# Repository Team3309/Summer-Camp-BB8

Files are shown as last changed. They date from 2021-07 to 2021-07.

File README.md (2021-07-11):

  
This work is licensed under a [Creative Commons Attribution-NonCommercial-ShareAlike 4.0 International License](http://creativecommons.org/licenses/by-nc-sa/4.0/).

# Overview

This is a remix of [DIY Machine's 3D printable BB8 robot](https://www.thingiverse.com/thing:2749613/files).

It replaces the stock Arduino Uno with an ESP32 DevKit and includes a reed switch to turn the robot on/off. In addition, a generic L298N motor controller board replaces the original motor shield

# Bill Of Materials

| Qty. | Name | Link |
| --- | --- | --- |
| 10 | 6 * 3mm Neodymium magnets | [Amazon](https://www.amazon.com/DIYMAG-6x3mm-Refrigerator-Premium-Brushed/dp/B07KZQGWNN/)
| 1 | Styrofoam hemisphere |
| 1 | Reed switch |
| 1 | L298N motor controller board |
| 1 | 3.3V Low-dropout regulator board |
| 1 | DOIT ESP32 DevKit v1 |
| 1 | 4*AA Battery harness |
| 2 | Geared 6v motors | [Amazon](https://www.amazon.com/Electric-Magnetic-Gearbox-Plastic-Yeeco/dp/B07DQGX369/) |
| 2 | 2.75in wheels | (included with motors) |
| 2-4 | .25in 4-40 Machine screws |
| 1 | Can of white spray paint |
| 1-2 fl oz | White acrylic paint |
| | Assorted sharpies |
| 1 | Roll of clear gift wrap tape |
| ≥5 | Small zipties |
| ~1in<sup>2<sup> | Low friction PTFE tape |
| A few | Male-male wires |
| A few | Female-female wires |
| One of each | Printed parts | [CAD/STLs](https://github.com/Team3309/Summer-Camp-BB8/tree/main/CAD/STLs) |

# Assembly

## Step 0: Prepping shells and decoration

1. Sand the inside and outside of the shells so that the chassis and head can both slide freely on them

2. Spray paint the outside of the shells

3. Hotglue the styrofoam hemisphere to the head, then use white acrylic paint to coat the assembly

4. Use the stand as a stencil to sharpie BB8 patterns onto the shell

## Step 1: Installing motors and motor controller

1. As shown in DIY Machines' video, put the motors in the chassis and secure them with zip ties

2. Ziptie the motor controller bracket to the neck/mast of the chassis

3. Use the screws to secure the motor controller **with the heatsink facing down**

## Step 2: Installing the reed switch

1. Use the jaws of a pair of calipers to gently bend the leads of the reed switch
    - Make sure the side with the circle artifacts from the injection mold is facing away from the leads

2. Solder a pair of wires (any color, preferably red) to the leads
    - They should be about 4 inches long, better to make it long and cut later

3. Insert the reed switch into the slot on the top of the neck/mast. **Be careful not to bend the leads**, lest you risk breaking the fragile reeds inside

## Step 3: Wiring and cable management

1. Connect the components according to the wiring diagram
    - To connect multiple wires to the screw terminals on the motor controller, strip the ends of the wires and twist them together
    - The GND pin of the LDO needs to be connected directly to the GND pin on the ESP32 board
        - If negative from the battery, GND on the LDO, and GND on the ESP32 are connected with separate wires to the GND terminal of the motor controller, then electrical noise causes the ESP32 to intermittently shut off, which is bad (duh)
        - To solve that issue, strip the opposite end of the wire that is connected to the ESP32's ground pin and (gently) shove that end into the connector on the LDO's ground pin, then put that connector back on the LDO pin

2. Use a ziptie to secure the ESP32 board to the chassis ***TODO: example photo***

3. Do your best to round up all the cables so that none touch the wheels or shell of the robot

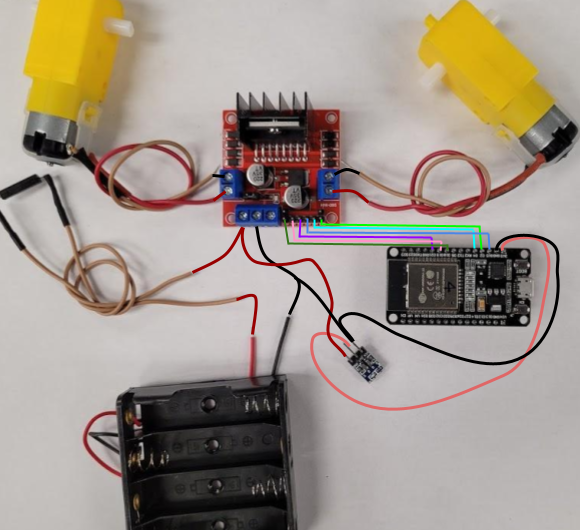
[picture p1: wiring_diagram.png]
Wiring Diagram

[Source for the above image](https://docs.google.com/presentation/d/1EXfWSO4wvMNs9FQZjlcnMrIVXtP51tsHmDwQ05yeIWY/edit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)

## Step 4: Installing neck and head magnets

1. Glue (try superglue if possible) two magnets in each slot on top of the neck
    - Make sure that they are all in the same orientation

2. Place small squares of PTFE tape on each exposed magnet

3. Put a half of the shell on top of the neck, then put a piece of wax paper

4. Stick three magnets to the ones in the neck (through the shell)

5. Apply hot glue to those magnets, then **quickly**, before the glue cools, place the head as straight as possible, facing forward

6. Once the magnets on the head are securely in place, glue another one in between the two in the front of the head
    - This is to trigger the reed switch when the head is in place

7. After the glue has fully cooled, place small squares of PTFE tape on each exposed magnet

## Step 5: Flash ESP32 board

- See /Code/README.md

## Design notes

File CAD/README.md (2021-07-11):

# 3D Printed Parts

| Qty. | Name | Source file | Notes |
| ---- | ---- | --- | ----- |
| 1 | BB8 Chassis | [Tinkercad](https://www.tinkercad.com/things/54Emxx3GyOb) (See below) |
| 1 | Motor Controller Bracket | [Onshape]()
| 1 | Grooved_Half_V2 | None |
| 1 | Tounged_Half_V2 | None |
| 1 | Head_V6_modified | [Autodesk Inventor](https://github.com/Team3309/Summer-Camp-BB8/tree/main/CAD/Source/Head_V6_Modified.ipt)
| 1 | Sensor | none | Optional, used as decoration on the head |
| 1 | Eye | none | Optional, used as decoration on the head |

<iframe width="725" height="453" src="https://www.tinkercad.com/embed/54Emxx3GyOb?editbtn=1" frameborder="0" marginwidth="0" marginheight="0" scrolling="no"></iframe>

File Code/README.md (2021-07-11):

# Flashing instructions

## Step 1: Setting up Arduino IDE

1. Download and install the [Arduino IDE](https://www.arduino.cc/en/software)

2. Go to **File > Preferences** (or press ctrl+,) and paste "https://dl.espressif.com/dl/package_esp32_index.json" into the "Additional Board Manager URLs" field, then click "OK"

3. Go to **Tools > Board > Boards Manager**, use the search bar on the top to find "esp32" and install **"esp32 by Espressif Systems"**

4. Go to **Tools > Manage Libraries...** and search "Dabble", then install "**DabbleESP32**"
    - The plain "Dabble" library will not work in this case, you must use "DabbleESP32"

5. Download [this](https://github.com/ERROPiX/ESP32_AnalogWrite/archive/refs/heads/master.zip) library, then go to **Sketch > Include Library > Add .ZIP Library...** and navigate to and select the the .zip archive that just downloaded

## Step 2: Flashing the board

1. Download and open (**File > Open**) ["BB8_dabble.ino"](https://github.com/Team3309/Summer-Camp-BB8/blob/main/Code/BB8_dabble.ino)
    - Optionally, find `Dabble.begin("BB8_xx");` and change the contents of the `""` to be whatever you want the robot to appear as on the pairing screen

2. Make sure that noting is powering the robot by removing one of the batteries

3. Go to **Tools > Board** and select **DOIT ESP32 DEVKIT V1**

4. Plug the ESP32 board into your computer with a micro-USB cable

5. Go to **Tools > Port** and select "COMx"
    - If there are multiple COM ports, you may need to use trial and error to find the right one (i.e continue with the next steps and if you get errors like "board not found", then switch ports and try again)

6. If you did everything correctly, then when you press the checkmark in the top left corner, the code should compile with no errors.

7. If it compiled with no problems, then flash the code onto the ESP32 by clicking the "upload" (arrow) button directly next to the checkmark

## Step 3: It's alive!

1. Unplug the USB cable, then power on the robot by replacing the batteries and putting the head in place on the neck

2. Download the Dabble app on your phone if you haven't done so already ([iOS](https://apps.apple.com/us/app/dabble-bluetooth-controller/id1472734455), [Android](https://play.google.com/store/apps/details?id=io.dabbleapp))

3. Launch the app and press the pair button (a plug and socket) in the top right corner

4. Find "BB8_xx" and pair to that, then open the "Controller" screen

5. Press the up button on the controller
    - The reed switch is in the front of the robot
    - If the left wheel spins backward, then change `#define LEFT_MOTOR_INVERTED false` to `#define LEFT_MOTOR_INVERTED true` and flash the updated code onto the ESP32 board again
    - If the right wheel spins backward, then change `#define RIGHT_MOTOR_INVERTED false` to `#define RIGHT_MOTOR_INVERTED true` and flash the updated code onto the ESP32 board again
    - Alternatively, switch the polarity of the inverted motor(s)

6. Press the right button on the controller
    - If the left wheel spins backward and the right wheel spins forward (i.e. robot spins counterclockwise), then move the wires from the left and right motors to the opposite set of terminals on the motor controller and repeat the last step

7. Finally, put the robot chassis inside the shells and tape them closed. Then attach the head to the top of the robot to power it on
    - Chances are that the reed switch will not stay reliably closed and the robot will loose connection as soon as it moves at all. In that case, tape/glue annother magnet on top of the reed switch so that it is always triggered

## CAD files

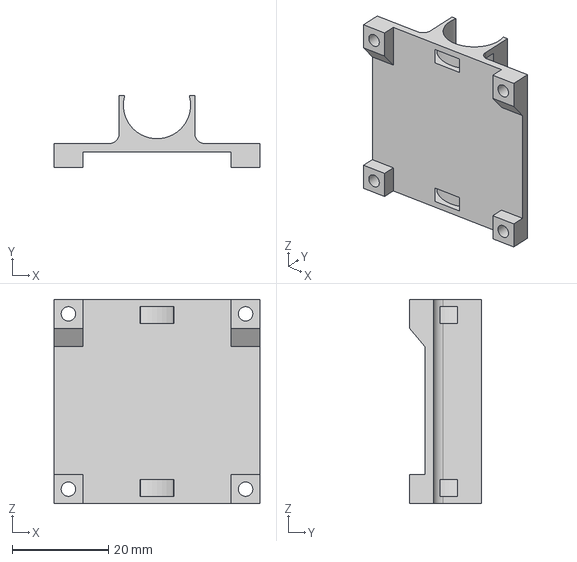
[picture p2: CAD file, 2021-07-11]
CAD/STEP/Motor Controller Bracket.step
42.9 x 15.0 x 42.5 mm

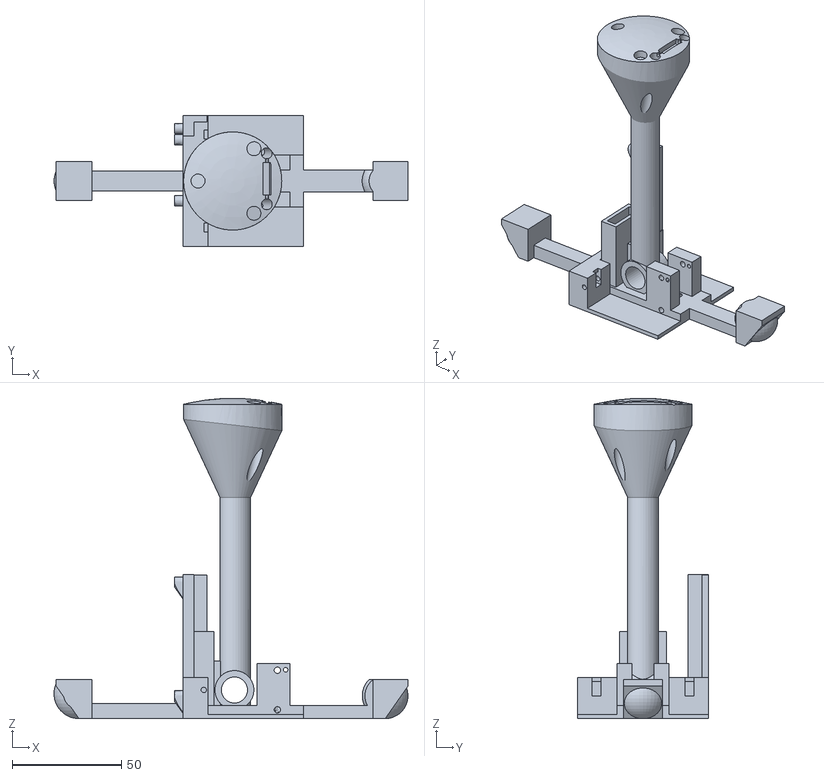
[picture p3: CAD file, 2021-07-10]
CAD/STL/BB8 Chassis.stl
162.2 x 60.0 x 146.8

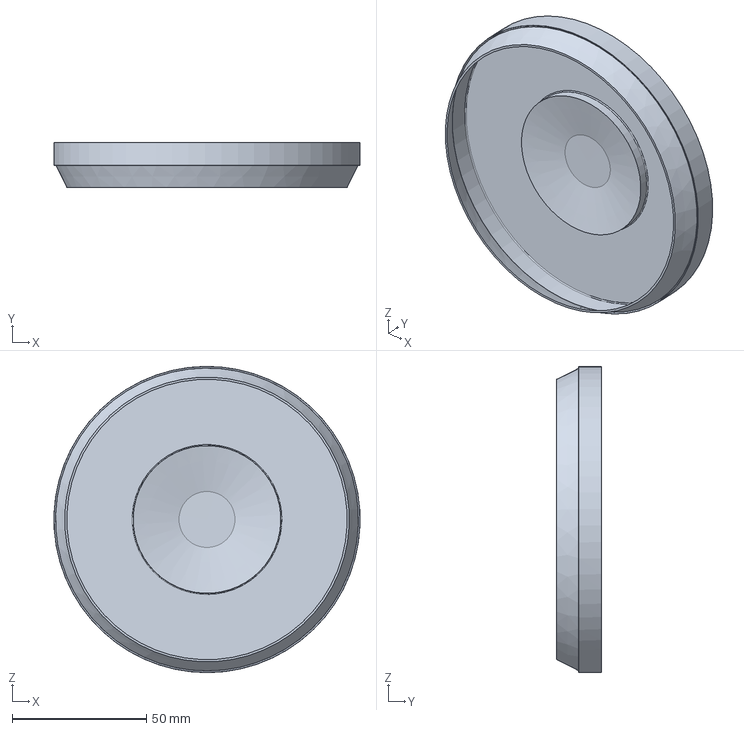
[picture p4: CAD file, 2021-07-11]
CAD/STEP/Head_V6_modified.step
113.9 x 16.9 x 114.0 mm

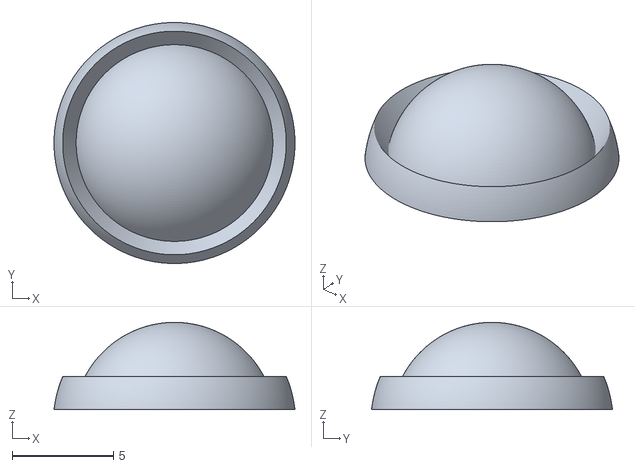
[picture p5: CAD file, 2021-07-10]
CAD/STL/Sensor.STL
11.9 x 11.9 x 4.32

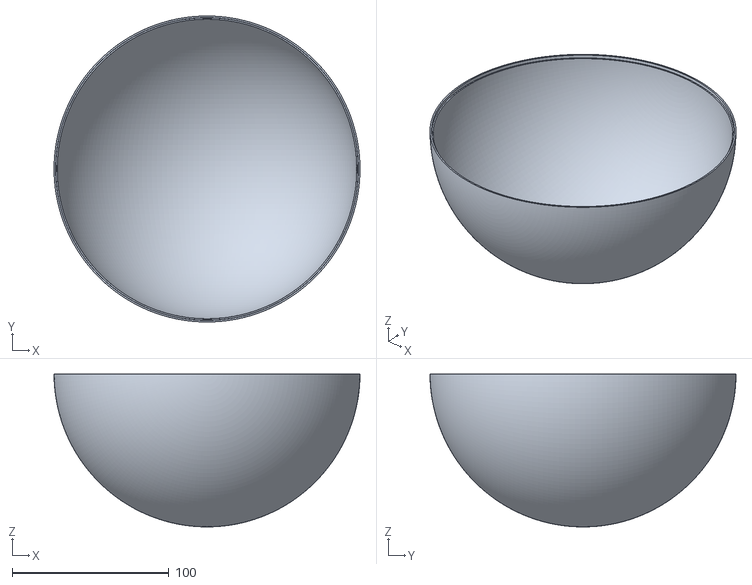
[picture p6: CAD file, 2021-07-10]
CAD/STL/Grooved_Half_V2.STL
195.0 x 195.0 x 97.4

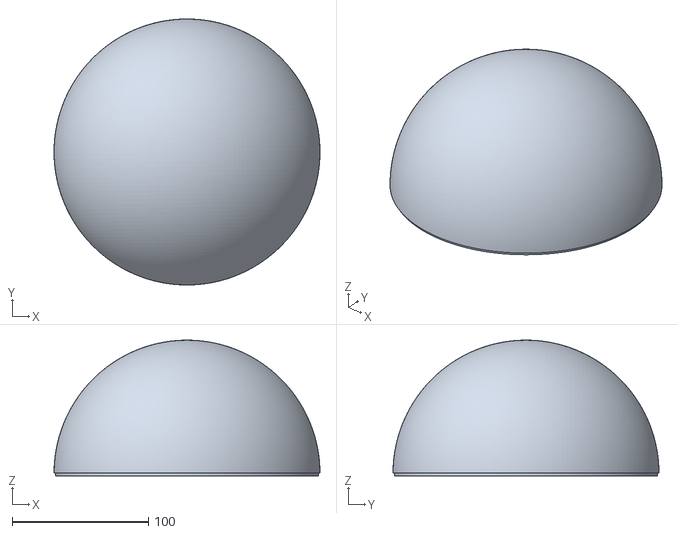
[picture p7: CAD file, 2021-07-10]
CAD/STL/Tounged_Half_V2.STL
195.0 x 195.0 x 99.5

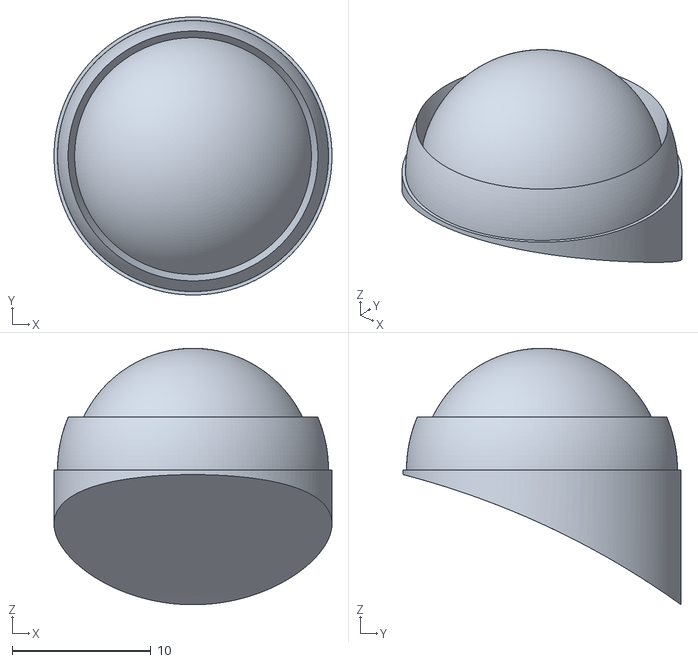
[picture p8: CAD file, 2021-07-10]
CAD/STL/Eye.STL
20.0 x 20.0 x 18.4

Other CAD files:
CAD/STL/Head_V6_modified.stl
CAD/STL/Motor Controller Bracket.stl
CAD/Source/Head_V6_modified.ipt

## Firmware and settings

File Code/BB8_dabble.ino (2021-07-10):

#include <Arduino.h>
#include <analogWrite.h>

// Import the Dabble libraries
#define CUSTOM_SETTINGS
#define INCLUDE_GAMEPAD_MODULE
#include <DabbleESP32.h>

//When ESP 32 faces the user, Motor1 is on the right side(port1)
// Motor1 Low, High = forward
// Motor2 High, Low = forward
#define ENA 18//4
#define IN1 19//2
#define IN2 21//15
#define IN3 15//21
#define IN4 4 //19
#define ENB 2//18

#define LEFT_MOTOR_INVERTED false
#define RIGHT_MOTOR_INVERTED false

void setup() {
  // Start bluetooth. This is where the ESP32's bluetooth name is declared
  Dabble.begin("BB8_xx");

  // Define pin functions
  pinMode(ENA, OUTPUT);
  pinMode(IN1, OUTPUT);
  pinMode(IN2, OUTPUT);
  pinMode(ENB, OUTPUT);
  pinMode(IN3, OUTPUT);
  pinMode(IN4, OUTPUT);
}

void loop() {
  // Get data from phone
  Dabble.processInput();

  // Get the joystick values from Dabble
  float dabbleX = GamePad.getXaxisData();
  float dabbleY = GamePad.getYaxisData();

  // The Dabble gamepad joystick returns values from -7 to 7, but we need -255 to 255, so do some math to convert
  int joyX = (int) (dabbleX * (255/7) + .5);
  int joyY = (int) (dabbleY * (255/7) + .5);

  if (GamePad.isUpPressed()) {
    joyY = 255;
  }
  if (GamePad.isDownPressed()) {
    joyY = -255;
  }
  if (GamePad.isLeftPressed()) {
    joyX = -255;
  }
  if (GamePad.isRightPressed()) {
    joyX = 255;
  }

  setArcadeSpeeds(joyY, joyX);
}

void setArcadeSpeeds (float throttle, float turn) {
  throttle *= -1;
  setMotorSpeeds (throttle - turn, throttle + turn);
}

void setMotorSpeeds (int left, int right) {
  setLeftMotorSpeed(left);
  setRightMotorSpeed(right);
}

void setLeftMotorSpeed (int left) {
  if (LEFT_MOTOR_INVERTED) {
    left *= -1;
  }
  if (left > 0) {
    analogWrite(ENA, left);
    digitalWrite(IN1, LOW);
    digitalWrite(IN2, HIGH);
  } else if (left < 0) {
    analogWrite(ENA, left);
    digitalWrite(IN1, HIGH);
    digitalWrite(IN2, LOW);
  } else {
    analogWrite(ENA, 0);
    digitalWrite(IN1, HIGH);
    digitalWrite(IN2, HIGH);
  }
}

void setRightMotorSpeed (int right) {
  if (RIGHT_MOTOR_INVERTED) {
    right *= -1;
  }
  if (right > 0) {
    analogWrite(ENB, right);
    digitalWrite(IN3, HIGH);
    digitalWrite(IN4, LOW);
  } else if (right < 0) {
    analogWrite(ENB, right);
    digitalWrite(IN3, LOW);
    digitalWrite(IN4, HIGH);
  } else {
    analogWrite(ENB, 0);
    digitalWrite(IN3, HIGH);
    digitalWrite(IN4, HIGH);
  }
}

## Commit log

2021-07-10 Upload STLs
    [BB8 Chassis.stl, Eye.STL, Grooved_Half_V2.STL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]
2021-07-10 Add assembly instructions and motor controller bracket STL
    [Motor Controller Bracket.stl]
2021-07-11 Upload CAD files
    [BB8 Chassis.stl, Eye.STL, Grooved_Half_V2.STL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]

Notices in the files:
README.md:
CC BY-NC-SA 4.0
